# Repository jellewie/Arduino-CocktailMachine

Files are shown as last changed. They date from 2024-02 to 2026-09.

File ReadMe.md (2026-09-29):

# **Cocktail Mixer Machine**  
_A machine that can mix drinks_

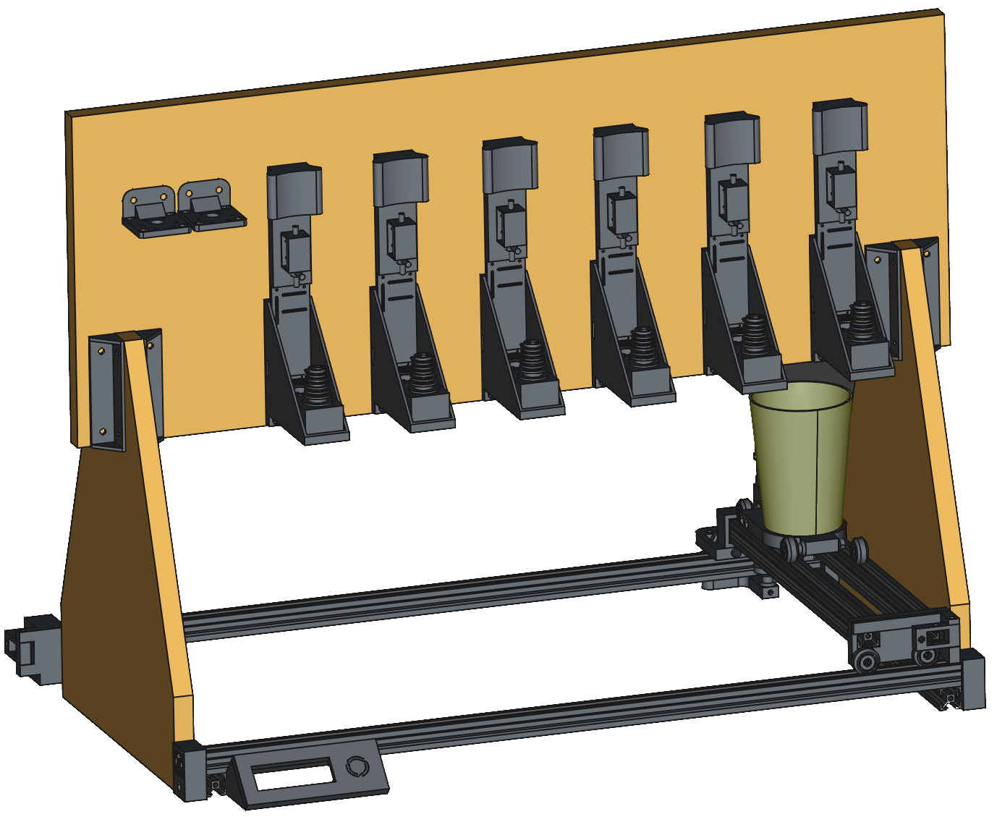
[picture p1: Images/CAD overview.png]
Cocktail Mixer Machine CAD


Part of this project is sponsored by [PCBWay](https://www.pcbway.com/). Read more about that [here](Sponsorship.md).

## **Firmware**
> **Note**: This project is still in development!

### Compile
- [Arduino sketch](Arduino) The whole sketch is the 'Arduino' folder.
- [ESP32](https://dl.espressif.com/dl/package_esp32_index.json) must be added as an additional board manager in Arduino IDE.
- [FastLED](https://github.com/FastLED/FastLED) can be downloaded through the built-in library manager in Arduino IDE.
- [AccelStepper](https://github.com/waspinator/AccelStepper) can be downloaded through the built-in library manager in Arduino IDE.
- [LiquidCrystal_I2C](https://github.com/johnrickman/LiquidCrystal_I2C) can be downloaded through the built-in library manager in Arduino IDE.
- [Deno](https://deno.land/) to re-compile the webpage.
- [Arduino-WIFIManager](https://github.com/jellewie/Arduino-WiFiManager) (already included).
- [Arduino-Button](https://github.com/jellewie/Arduino-Button) (already included).
- [Arduino-Stable-analog-read](https://github.com/jellewie/Arduino-Stable-analog-read) (already included).
- [FreeCAD](https://github.com/FreeCAD/FreeCAD) is used for 3D modeling.
- [A2Plus_Workbench](https://github.com/kbwbe/A2plus) is used for creating the assembly.

To custom compile with new drinks and such, update the drinks in [Website/src/drinksConfig.js](Website/src/drinksConfig.js). I use an automated Google Drive sheet for this.

To update the Arduino to use this, run "deno task build" in the command prompt. This will update the client.h, after which you can start Arduino IDE and use it.

### BIN
Uploading a BIN file with a cable to the ESP can be done by any [ESP32 BIN file uploader](https://www.espressif.com/en/support/download/other-tools). this step is required for the first flash time.

## Webpage
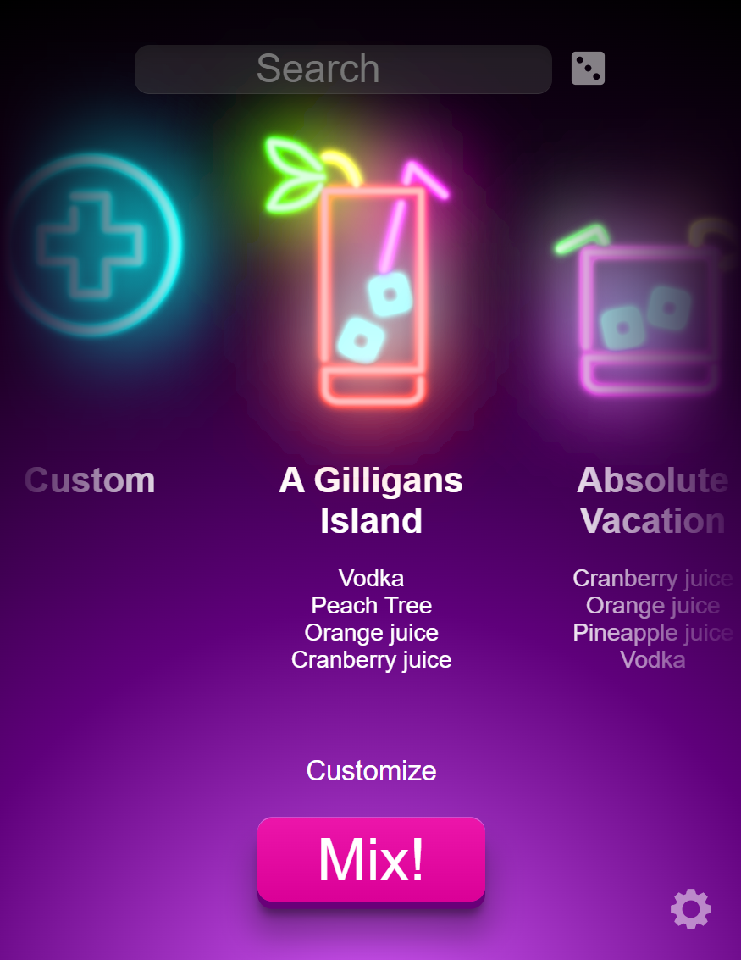
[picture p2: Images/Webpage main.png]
The landing webpage of the machine

The machine makes its own fancy landing page. This page has a lot going for it, First of all, are the items sorted on last used (this is done locally per user device). But the page has also a lot of functions, for example, it has a search bar to search for the name, but it also has a dice function to select a random mix.

After you have chosen your mix, you can directly start mixing, or you can Customize the drink to your liking

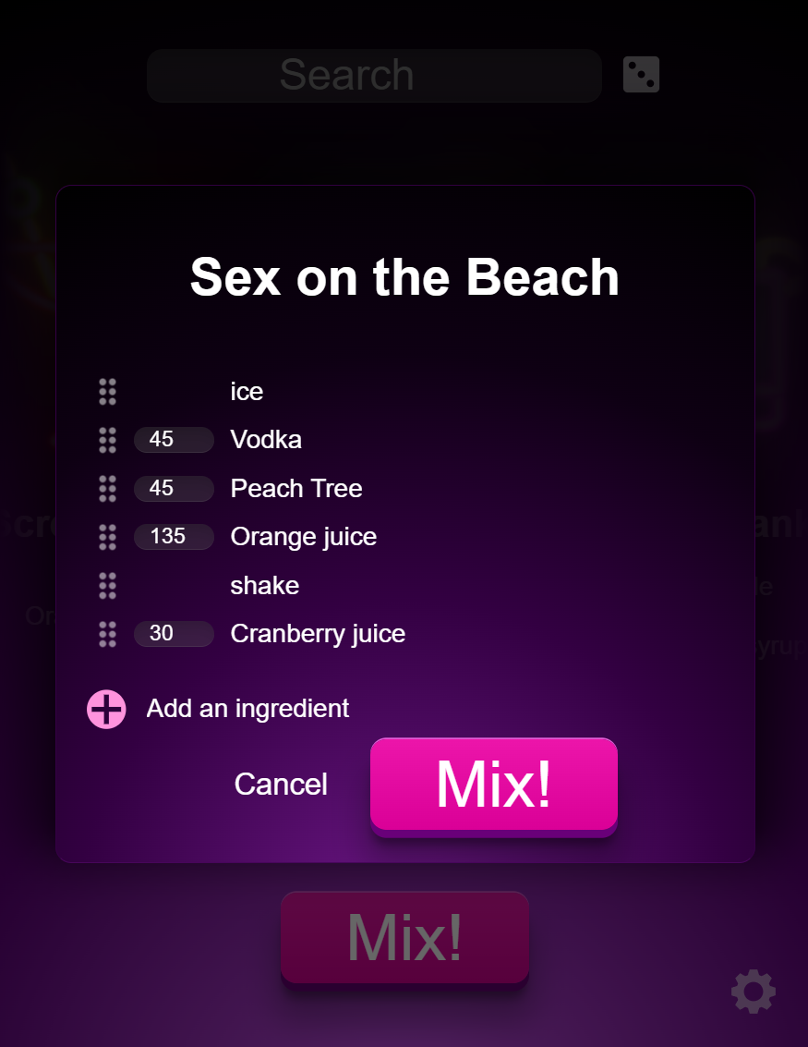
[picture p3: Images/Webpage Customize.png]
Customize drink

It also has a settings page

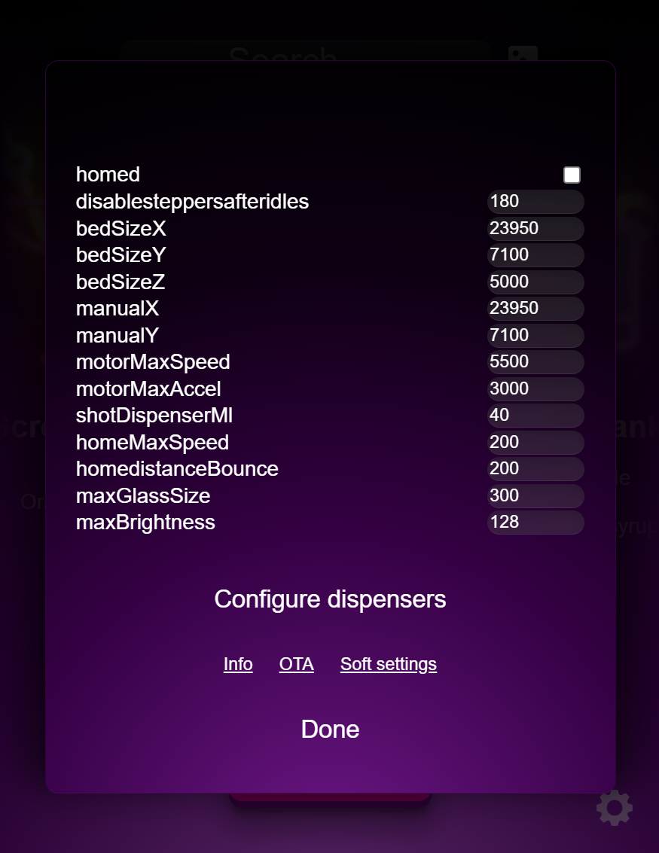
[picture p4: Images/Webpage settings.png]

This is also where the dispensers are configured

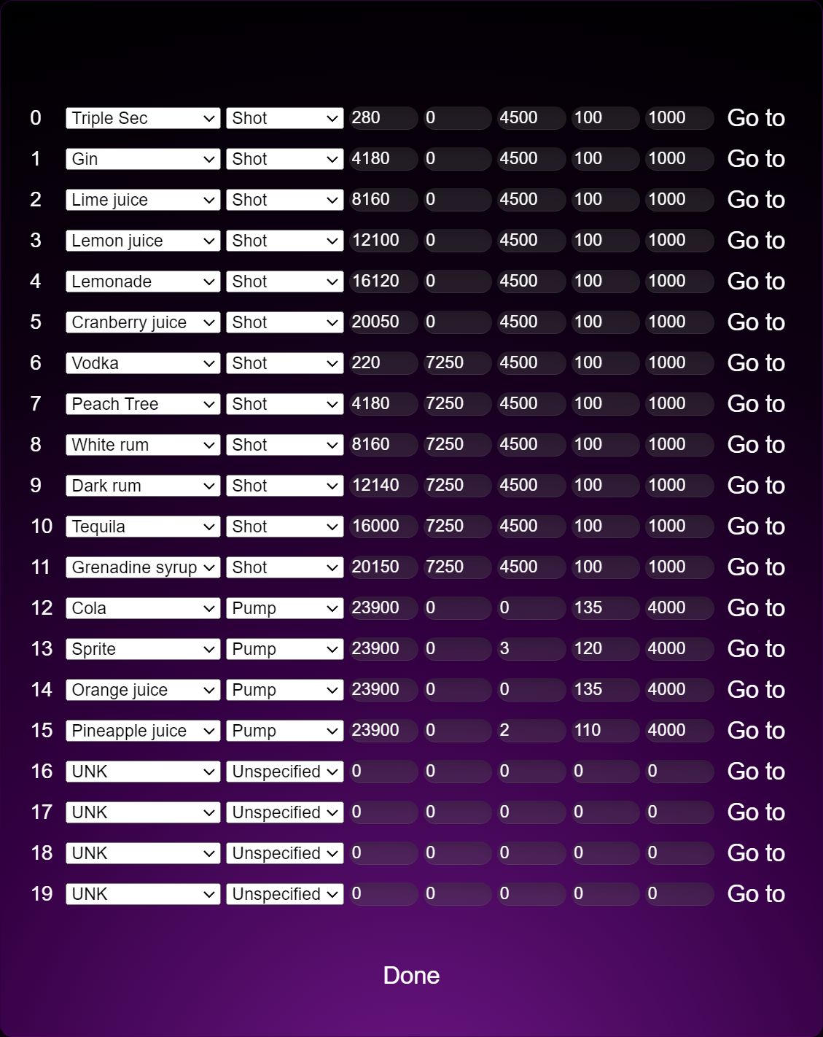
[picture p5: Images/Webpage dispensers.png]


## LED status

## WIFI page
The 2 most important pages are the [Setup](#setup) page, where the user can set up the mixer. And the [main landing page](#control) where the fancy UI is.
Setup is only really needed once during the setup of WiFi in Apmode, because in runtime the mixer settings can be adjusted in the main UI.

### Setup
The setup page will be accessible and shown in APmode, but can also be accessed by going to [mixer.local/ip](http://mixer.local/ip). 
The password is replaced with starts, and cannot be received without changing the firmware. 
Leave fields blank (or for the password leaving only stars) to not update those values upon sending this forum, set on space ' ' to clear them.
By default the SSID and password are limited to 16 characters by the firmware, and the total bytes that can be stored in memory is limited to 4096. Going over these values results in unexpected behavior. 

### Getting it’s IP
User devices that support mDNS, like Windows and Apple, can use [mixer.local/info](http://mixer.local/info) to obtain its IP.

Alternatively in a lot of stages (like after boot) the IP will be shown on the display.

### Control
The control page is the default landing page the user will land on. Here you select, customize, and mix the selected drink. 

- **customize** Will give a pop-up window to customize and mix your drink.
- **MIX** Will start mixing it right away.
- **Settings button** The gear on the right lower corner will open the settings page.

#### Settings button
- Some [Soft settings](#Soft-settings) are exposed here
- **OTA** will direct to the [OTA](#ota-over-the-air-update) update page, where the firmware can be updated over the WiFi.
- **Reset** will fully restart the ESP.
- **Info** will open the info page with some information like the version compile date.
- **Saved settings** just redirects you to [mixer.local/ip](http://mixer.local/ip) to show you the values saved in the EEPROM.

### Soft settings

### OTA (Over The Air update)
This page can be accessed on [mixer.local/ota](http://mixer.local/ota) (or 'IP/ota') and enables you to update firmware over WiFi.
On this page is a 'choose file' button where the new version can be selected. Make sure the right, compatible, most updated file is selected ("Mixer.bin"). This can be downloaded from [releases](https://github.com/jellewie/Arduino-CocktailMachine/releases). 
After which the 'Upload' button needs to be pressed for the update process to begin, the unit will automatically update and reboot afterward.
Note that [SoftSettings](#soft-settings) are preserved.

### Full reset
If a full reset is desired it can be achieved by going to 'mixer.local/reset'. But note that accessing the page will directly wipe all [SoftSettings](#soft-settings) from existence and there will be no way to restore them back. If the wipe was successful it will be reported back and will execute a restart.

# Appendix
* Firmware
[This is included in this repository](Arduino)
* PCB & schematic
[This is included in this repository](Schematic-PCB)
Beta/ updated version on [EasyEDA](https://easyeda.com/selbiekoekie/cocktail-machine)
* BOM
[This is included in this repository](BOM.md)

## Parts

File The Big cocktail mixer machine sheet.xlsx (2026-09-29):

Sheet: BOM
Description | Amount | Comments | Link buy | Link info | Piece price | Shipping | Total | |Description|Amount|Comments|Link buy|Link info|Piece price|Shipping|Total
--- | --- | --- | --- | --- | --- | --- | --- | |---|---|---|---|---|---|---|---
Peristaltic Pump,12V (We use zy-1000f5) | 4 | Only needed for carbonated liquids | https://www.banggood.com/500mL-or-min-Large-Flow-Easy-To-Install-Peristaltic-Pump-12V-or-24V-Metering-Vacuum-Pump-Flat-Type-Aquarium-p-1749029.html https://nl.aliexpress.com/item/1005004441796531.html | https://youtu.be/AMiXme4bMUk | €25.95 | €1.62 | €105.40 | |Peristaltic Pump,12V (We use zy-1000f5)|4|Only needed for carbonated liquids|[link](https://www.banggood.com/500mL-or-min-Large-Flow-Easy-To-Install-Peristaltic-Pump-12V-or-24V-Metering-Vacuum-Pump-Flat-Type-Aquarium-p-1749029.html https://nl.aliexpress.com/item/1005004441796531.html|[link](https://youtu.be/AMiXme4bMUk)|25.95|1.62|105.4
Pullys | 2 |  | https://www.123-3d.nl/123-3D-GT2-Pulley-hoge-resolutie-met-lager-6-mm-riem-20-tanden-5-mm-as-zwart-i2546-t0.html |  | €7.50 | €0.71 | €15.71 | |Pullys|2||[link](https://www.123-3d.nl/123-3D-GT2-Pulley-hoge-resolutie-met-lager-6-mm-riem-20-tanden-5-mm-as-zwart-i2546-t0.html)||7.5|0.71|15.71
Motor pullys | 2 |  | https://www.123-3d.nl/123-3D-GT2-Pulley-hoge-resolutie-6-mm-riem-20-tanden-5-mm-as-zwart-400211009-i2547-t0.html |  | €7.50 | €0.71 | €15.71 | |Motor pullys|2||[link](https://www.123-3d.nl/123-3D-GT2-Pulley-hoge-resolutie-6-mm-riem-20-tanden-5-mm-as-zwart-400211009-i2547-t0.html)||7.5|0.71|15.71
Reininforced belt 6mm wide | 1 | 2.7m needed | https://www.123-3d.nl/123-3D-GT2-timing-belt-6-mm-5-meter-i6541-t3046.html |  | €21.00 | €0.71 | €21.71 | |Reininforced belt 6mm wide|1|2.7m needed|[link](https://www.123-3d.nl/123-3D-GT2-timing-belt-6-mm-5-meter-i6541-t3046.html)||21|0.71|21.71
Leadscrew moer, TR8x8 | 1 |  | https://www.123-3d.nl/123-3D-Leadscrew-moer-TR8x8-i1560-t0.html |  | €6.00 | €0.71 | €6.71 | |Leadscrew moer, TR8x8|1||[link](https://www.123-3d.nl/123-3D-Leadscrew-moer-TR8x8-i1560-t0.html)||6|0.71|6.71
Leadscrew, TR8x8, 8 mm | 1 | This one is 30cm, unsure what we need | https://www.123-3d.nl/123-3D-Leadscrew-TR8x8-8-mm-30-cm-i1558-t0.html |  | €9.50 | €0.71 | €10.21 | |Leadscrew, TR8x8, 8 mm|1|This one is 30cm, unsure what we need|[link](https://www.123-3d.nl/123-3D-Leadscrew-TR8x8-8-mm-30-cm-i1558-t0.html)||9.5|0.71|10.21
Staaf as glad 8 m | 1 | This one is 100cm, unsure what we need | https://www.123-3d.nl/123-3D-Staaf-as-glad-8-mm-x-100-cm-voor-X-of-Y-as-i56-t0.html |  | €3.75 | €0.71 | €4.46 | |Staaf as glad 8 m|1|This one is 100cm, unsure what we need|[link](https://www.123-3d.nl/123-3D-Staaf-as-glad-8-mm-x-100-cm-voor-X-of-Y-as-i56-t0.html)||3.75|0.71|4.46
Flexibele motor koppeling 5 mm - 8 mm | 1 |  | https://www.123-3d.nl/123-3D-Flexibele-motor-koppeling-5-mm-8-mm-i342-t0.html |  | €4.50 | €0.71 | €5.21 | |Flexibele motor koppeling 5 mm - 8 mm|1||[link](https://www.123-3d.nl/123-3D-Flexibele-motor-koppeling-5-mm-8-mm-i342-t0.html)||4.5|0.71|5.21
Frame end caps 2020 (3d print) | 10 | Print in black |  | https://www.thingiverse.com/thing:2393904 | €0.02 | €0.00 | €0.20 | |Frame end caps 2020 (3d print)|10|Print in black||[link](https://www.thingiverse.com/thing:2393904)|0.02|0|0.2
Drink dispensers (6 way) | 2 | Spraypaint black | https://www.bol.com/nl/nl/p/white-rhinoceros-drank-dispenser-bar-butler-shots-muurdispenser-voor-6-flessen/9300000007705748/ |  | €38.95 | €0.00 | €77.90 | |Drink dispensers (6 way)|2|Spraypaint black|[link](https://www.bol.com/nl/nl/p/white-rhinoceros-drank-dispenser-bar-butler-shots-muurdispenser-voor-6-flessen/9300000007705748/||38.95|0|77.9
V frame (black 1500mm) | 2 | Cut in sizes: 2x750 + 2x353.5 + 2x396.5mm | https://www.ratrig.com/aluminium-profiles/vslot/v-slot-2020-637.html |  | €12.54 | €28.52 | €53.60 | |V frame (black 1500mm)|2|Cut in sizes: 2x750 + 2x353.5 + 2x396.5mm|[link](https://www.ratrig.com/aluminium-profiles/vslot/v-slot-2020-637.html)||12.54|28.52|53.6
Frame corner profiles | 20 |  | https://nl.aliexpress.com/item/1005003618509458.html |  | €0.50 | €2.43 | €12.45 | |Frame corner profiles|20||[link](https://nl.aliexpress.com/item/1005003618509458.html)||0.5|2.43|12.45
Wood (Gamma) | 1 | 2x30x80cm |  |  | €30.48 | €0.00 | €30.48 | |Wood (Gamma)|1|2x30x80cm|||30.48|0|30.48
16x2 LCD Display I2C | 1 |  | https://elektronicavoorjou.nl/product/16x2-lcd-wit-op-blauw-5v-met-i2c/ |  | €9.95 | €2.99 | €12.94 | |16x2 LCD Display I2C|1||[link](https://elektronicavoorjou.nl/product/16x2-lcd-wit-op-blauw-5v-met-i2c/)||9.95|2.99|12.94
M3x10 | 50 |  | https://www.indi.nl/nl-nl/p/Cilindrische-inbusbout-M3x10-12.9-zwart-DIN912-912310129B |  | €0.17 | €1.40 | €10.02 | |M3x10|50||[link](https://www.indi.nl/nl-nl/p/Cilindrische-inbusbout-M3x10-12.9-zwart-DIN912-912310129B)||0.17|1.4|10.02
M3x30 | 50 |  | https://www.indi.nl/nl-nl/p/Cilindrische-inbusbout-M3x30-12.9-zwart-DIN912-912330129B |  | €0.17 | €1.40 | €10.02 | |M3x30|50||[link](https://www.indi.nl/nl-nl/p/Cilindrische-inbusbout-M3x30-12.9-zwart-DIN912-912330129B)||0.17|1.4|10.02
M5x10 | 50 |  | https://www.indi.nl/nl-nl/p/Cilindrische-inbusbout-M5x10-12.9-zwart-DIN912-912510129B |  | €0.18 | €1.40 | €10.40 | |M5x10|50||[link](https://www.indi.nl/nl-nl/p/Cilindrische-inbusbout-M5x10-12.9-zwart-DIN912-912510129B)||0.18|1.4|10.4
M5x20 | 50 |  | https://www.indi.nl/nl-nl/p/Cilindrische-inbusbout-M5x20-12.9-zwart-DIN912-912520129B |  | €0.18 | €1.40 | €10.40 | |M5x20|50||[link](https://www.indi.nl/nl-nl/p/Cilindrische-inbusbout-M5x20-12.9-zwart-DIN912-912520129B)||0.18|1.4|10.4
M5x30 | 50 |  | https://www.indi.nl/nl-nl/p/Cilindrische-inbusbout-M5x30-12.9-zwart-DIN912-912530129B |  | €0.18 | €1.40 | €10.40 | |M5x30|50||[link](https://www.indi.nl/nl-nl/p/Cilindrische-inbusbout-M5x30-12.9-zwart-DIN912-912530129B)||0.18|1.4|10.4
M5x40 | 50 |  | https://www.indi.nl/nl-nl/p/Cilindrische-inbusbout-M5x40-12.9-zwart-DIN912-912540129B |  | €0.27 | €1.40 | €14.90 | |M5x40|50||[link](https://www.indi.nl/nl-nl/p/Cilindrische-inbusbout-M5x40-12.9-zwart-DIN912-912540129B)||0.27|1.4|14.9
M5x50 | 50 |  | https://www.indi.nl/nl-nl/p/Cilindrische-inbusbout-M5X50-12.9-zwart-DIN912-912550129B |  | €0.34 | €1.40 | €18.40 | |M5x50|50||[link](https://www.indi.nl/nl-nl/p/Cilindrische-inbusbout-M5X50-12.9-zwart-DIN912-912550129B)||0.34|1.4|18.4
M5x60 | 50 |  | https://www.indi.nl/nl-nl/p/Cilindrische-inbusbout-M5x60-12.9-zwart-DIN912-912560129B |  | €0.39 | €1.40 | €20.72 | |M5x60|50||[link](https://www.indi.nl/nl-nl/p/Cilindrische-inbusbout-M5x60-12.9-zwart-DIN912-912560129B)||0.39|1.4|20.72
M5x80 | 50 |  | https://www.indi.nl/nl-nl/p/Cilindrische-inbusbout-M5x80-12.9-zwart-DIN912-912580129B |  | €0.84 | €1.40 | €43.16 | |M5x80|50||[link](https://www.indi.nl/nl-nl/p/Cilindrische-inbusbout-M5x80-12.9-zwart-DIN912-912580129B)||0.84|1.4|43.16
Moer | 200 |  | https://www.indi.nl/nl-nl/p/Zeskantmoer-M5-klasse-8-verzinkt-DIN934-9345P100 |  | €0.05 | €1.40 | €11.40 | |Moer|200||[link](https://www.indi.nl/nl-nl/p/Zeskantmoer-M5-klasse-8-verzinkt-DIN934-9345P100)||0.05|1.4|11.4
Borgmoer | 8 |  | https://www.gamma.nl/assortiment/gamma-borgmoer-m5-rvs-8-stuks/p/B458288 |  | €0.35 | €0.00 | €2.79 | |Borgmoer|8||[link](https://www.gamma.nl/assortiment/gamma-borgmoer-m5-rvs-8-stuks/p/B458288)||0.35|0|2.79
V-slot wheels | 11 |  |  |  | €0.71 | €0.00 | €7.83 | |V-slot wheels|11||||0.71|0|7.83
JLC PCB | 5 | (minimum 5 pieces) |  |  | €1.44 | €0.00 | €7.20 | |JLC PCB|5|(minimum 5 pieces)||[link]()|1.44|0|7.2
PCB-TMC2208 motor controller | 3 | X, Y, Z | https://nl.aliexpress.com/item/1005004014058136.html | https://wiki.fysetc.com/TMC2208/ | €2.49 | €0.00 | €7.46 | |PCB-TMC2208 motor controller|3|X, Y, Z|[link](https://nl.aliexpress.com/item/1005004014058136.html)|[link](https://wiki.fysetc.com/TMC2208/)|2.49|0|7.46
Microswitch | 3 | Used for homing, not as limit switch | https://www.hobbyelectronica.nl/product/endstop-mechanisch-microswitch/ |  | €0.95 | €3.45 | €6.30 | |Microswitch|3|Used for homing, not as limit switch|[link](https://www.hobbyelectronica.nl/product/endstop-mechanisch-microswitch/)||0.95|3.45|6.3
Tubing 5x7 | 6 |  | https://www.kiwi-electronics.com/nl/siliconen-slang-5x7mm-2-meter-10188 |  | €1.95 | €2.95 | €14.65 | |Tubing 5x7|6||[link](https://www.kiwi-electronics.com/nl/siliconen-slang-5x7mm-2-meter-10188)||1.95|2.95|14.65
Tubing 2x4 | 14 |  | https://www.slangenshop.nl/home/22-siliconen-slang-2-x-4-mm-.html |  | €2.22 | €7.95 | €39.03 | |Tubing 2x4|14||[link](https://www.slangenshop.nl/home/22-siliconen-slang-2-x-4-mm-.html)||2.22|7.95|39.03
Tubing 3x5 | 7 |  | https://www.slangenshop.nl/home/25-siliconen-slang-3-x-5-mm-.html |  | €3.88 | €6.95 | €34.11 | |Tubing 3x5|7||[link](https://www.slangenshop.nl/home/25-siliconen-slang-3-x-5-mm-.html)||3.88|6.95|34.11
Tubing 4x6 | 7 |  | https://www.slangenshop.nl/home/24-siliconen-slang-4-x-6-mm-.html?search_query=Siliconen+slang+4&results=24 |  | €3.81 | €7.95 | €34.62 | |Tubing 4x6|7||[link](https://www.slangenshop.nl/home/24-siliconen-slang-4-x-6-mm-.html?search_query=Siliconen+slang+4&results=24)||3.81|7.95|34.62
0826B 0.5-20N 8mm | 1 |  | https://www.aliexpress.com/item/1005004016711403.html?spm=a2g0o.cart.0.0.603638daNtRRN5&mp=1 |  | €8.54 |  | €8.54 | |0826B 0.5-20N 8mm|1||[link](https://www.aliexpress.com/item/1005004016711403.html?spm=a2g0o.cart.0.0.603638daNtRRN5&mp=1)||8.54||8.54
1050B 4.5-50N 15mm | 1 |  | https://www.aliexpress.com/item/1005004016711403.html?spm=a2g0o.cart.0.0.603638daNtRRN5&mp=1 |  | €16.36 |  | €16.36 | |1050B 4.5-50N 15mm|1||[link](https://www.aliexpress.com/item/1005004016711403.html?spm=a2g0o.cart.0.0.603638daNtRRN5&mp=1)||16.36||16.36
Motion Film Pressure Sensor 100g | 1 |  | https://www.aliexpress.com/item/32878178151.html?spm=a2g0o.cart.0.0.603638daNtRRN5&mp=1 |  | €1.31 | €0.80 | €2.10 | |Motion Film Pressure Sensor 100g|1||[link](https://www.aliexpress.com/item/32878178151.html?spm=a2g0o.cart.0.0.603638daNtRRN5&mp=1)||1.31|0.8|2.11
Motion Film Pressure Sensor 1kg | 1 |  | https://www.aliexpress.com/item/32878178151.html?spm=a2g0o.cart.0.0.603638daNtRRN5&mp=1 |  | €1.31 | €0.80 | €2.10 | |Motion Film Pressure Sensor 1kg|1||[link](https://www.aliexpress.com/item/32878178151.html?spm=a2g0o.cart.0.0.603638daNtRRN5&mp=1)||1.31|0.8|2.11
Solenoid Valve 4.5mm inner 12V | 1 |  | https://www.aliexpress.com/item/1005005553905520.html?spm=a2g0o.cart.0.0.603638daNtRRN5&mp=1 |  | €3.34 | €3.61 | €6.95 | |Solenoid Valve 4.5mm inner 12V|1||[link](https://www.aliexpress.com/item/1005005553905520.html?spm=a2g0o.cart.0.0.603638daNtRRN5&mp=1)||3.34|3.61|6.95
CNC W202502152128202 | 1 |  |  |  | €39.93 |  | €39.93 | |CNC W202502152128202|1||||39.93||39.93
CNC W202410082342933 |  |  |  |  | €43.10 |  | €0.00 | |CNC W202410082342933|||||43.1||0
CNC CNC2403305000117-2352374A |  |  |  |  | €19.99 |  | €0.00 | |CNC CNC2403305000117-2352374A|||||19.99||0
 |  |  |  |  |  |  | €0.00
 |  |  |  |  |  |  | €0.00
 |  |  |  |  |  |  | €0.00
 |  |  |  |  |  |  | €0.00
SUBTOTAAL |  |  |  |  |  |  | €762.48
Steppermotor | 3 | We actually use 1.8deg 2.4Ohm | https://www.hobbyelectronica.nl/product/nema-17-stappen-motor-42byghw609/ |  | €22.62 | €6.95 | €74.81 | |Steppermotor|3|We actually use 1.8deg 2.4Ohm|[link](https://www.hobbyelectronica.nl/product/nema-17-stappen-motor-42byghw609/||22.62|6.95|74.81
Connector MTA-100-2P | 7 |  |  |  | €0.15 |  | €1.04 | |Connector MTA-100-2P|7|||[link]()|0.15||1.04
Connector MTA-100-3P | 1 |  |  |  | €0.14 |  | €0.14 | |Connector MTA-100-3P|1|||[link]()|0.14||0.14
Connector MTA-100-4P | 4 |  |  |  | €0.23 |  | €0.94 | |Connector MTA-100-4P|4|||[link]()|0.24||0.94
Connector MTA-156-2P | 2 |  |  |  | €0.22 |  | €0.44 | |Connector MTA-156-2P|2||||0.22||0.44
PCB-MTA-100-2P | 7 | H2,H3,H4,H11,H12,H13,H14 |  |  | €0.10 |  | €0.73 | |PCB-MTA-100-2P|7|H2,H3,H4,H11,H12,H13,H14||[link]()|0.11||0.74
PCB-MTA-100-3P | 1 | for LED D=H5 | http://www.te.com/commerce/DocumentDelivery/DDEController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 |  | €0.07 |  | €0.07 | |PCB-MTA-100-3P|1|for LED D=H5|[link](http://www.te.com/commerce/DocumentDelivery/DDEController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)||0.07||0.07
PCB-MTA-100-4P | 4 | H8, H9, H10,H16 | http://www.te.com/commerce/DocumentDelivery/DDEController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 |  | €0.13 |  | €0.51 | |PCB-MTA-100-4P|4|H8, H9, H10,H16|[link](http://www.te.com/commerce/DocumentDelivery/DDEController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)||0.13||0.51
PCB-MTA-156-2P | 2 | H6, H7 |  |  | €0.10 |  | €0.21 | |PCB-MTA-156-2P|2|H6, H7||[link]()|0.11||0.21
PCB-L2203N | 4 | Q1,Q2,Q3,Q4 |  |  | €0.93 |  | €3.73 | |PCB-L2203N|4|Q1,Q2,Q3,Q4|[link]( )|[link]()|0.93||3.73
PCB-C0805 100nF | 6 | C1,C2,C3,C4,C5,C6 |  |  | €0.01 |  | €0.05 | |PCB-C0805 100nF|6|C1,C2,C3,C4,C5,C6|[link]( )|[link]()|0.01||0.05
PCB-R0805 1k | 7 | R1,R2,R3,R4,R5,R6,R7 |  |  | €0.01 |  | €0.05 | |PCB-R0805 1k|7|R1,R2,R3,R4,R5,R6,R7|[link]( )|[link]()|0.01||0.05
PCB-R0805 100R | 1 | R8 |  |  | €0.01 |  | €0.01 | |PCB-R0805 100R|1|R8|[link]( )|[link]()|0.01||0.01
PCB-R0805 10R | 1 | R9 |  |  | €0.01 |  | €0.01 | |PCB-R0805 10R|1|R9|[link]( )|[link]()|0.01||0.01
PCB-DOIT ESP32 DEVKIT V1 | 1 | U1 |  |  | €3.96 |  | €3.96 | |PCB-DOIT ESP32 DEVKIT V1|1|U1|[link]( )|[link]()|3.96||3.96
PCB-R78B5020 | 1 | U2 | https://nl.farnell.com/recom-power/r-78b5-0-1-0l/dc-dc-converter-5v-1a/dp/1793162 |  | €7.57 |  | €7.57 | |PCB-R78B5020|1|U2|[link](https://nl.farnell.com/recom-power/r-78b5-0-1-0l/dc-dc-converter-5v-1a/dp/1793162)||7.57||7.57
PCB-SIL header | 2 | Steppers, H1 |  |  | €0.06 | €0.00 | €0.12 | |PCB-SIL header|2|Steppers, H1||[link]()|0.06|0|0.12
12V power supply | 1 |  |  |  |  |  | €0.00 | |12V power supply|1||||||0
Wires |  |  |  |  |  |  | €0.00 | |Wires|||||||0
Wire sleeves? |  |  |  |  |  |  | €0.00 | |Wire sleeves?|||||||0
PCBway Dispensers | 13 |  |  |  | €85.36 |  | €1109.68 | |PCBway Dispensers|13|||[link]()|85.36||1109.68
0805 4.7UH | 50 |  | https://nl.aliexpress.com/item/1005006311167114.html |  |  |  | €0.00 | |0805 4.7UH|50||[link](https://nl.aliexpress.com/item/1005006311167114.html||||0
heatshrink | 2 |  | https://nl.aliexpress.com/item/1005006321995370.html |  | €1.79 |  | €3.58 | |heatshrink|2||[link](https://nl.aliexpress.com/item/1005006321995370.html||1.79||3.58
Diode IN4007 | 100 |  | www.aliexpress.com/item/1005006852412154.html?spm=a2g0o.order_list.order_list_main.33.3f8379d22lLZlI |  | €0.04 |  | €3.50 | |Diode IN4007|100||[link](www.aliexpress.com/item/1005006852412154.html||0.04||3.5
ESP32 C3 | 20 |  | https://nl.aliexpress.com/item/1005007446928015.html |  | €1.04 |  | €20.81 | |ESP32 C3|20||[link](https://nl.aliexpress.com/item/1005007446928015.html||1.04||20.81
Dispenser magnet | 25 |  | https://nl.aliexpress.com/item/1005006531774076.html |  | €2.69 |  | €67.20 | |Dispenser magnet|25||[link](https://nl.aliexpress.com/item/1005006531774076.html||2.69||67.2
O-rings dispenserbold | 675 |  | https://nl.aliexpress.com/item/1005008478445571.html |  | €0.01 |  | €8.82 | |O-rings dispenserbold|675||[link](https://nl.aliexpress.com/item/1005008478445571.html||0.01||8.82
M5 bolt 5mm | 20 |  | https://nl.aliexpress.com/item/32810872544.html |  | €0.11 |  | €2.18 | |M5 bolt 5mm|20||[link](https://nl.aliexpress.com/item/32810872544.html||0.11||2.18
M4 bolt 10mm | 60 |  | https://nl.aliexpress.com/item/32810872544.html |  | €0.07 |  | €4.04 | |M4 bolt 10mm|60||[link](https://nl.aliexpress.com/item/32810872544.html||0.07||4.04
M3 bolt 5mm | 200 |  |  |  | €0.02 |  | €4.04 | |M3 bolt 5mm|200||||0.02||4.04
Capacitor 47uF | 50 |  | www.aliexpress.com/item/1005002047657907.html |  | €0.04 |  | €2.15 | |Capacitor 47uF |50||[link](www.aliexpress.com/item/1005002047657907.html||0.04||2.15
8 DIP header | 60 |  | https://www.aliexpress.com/item/1005006995121970.html |  | €0.03 |  | €1.51 | |8 DIP header|60||[link](https://www.aliexpress.com/item/1005006995121970.html||0.03||1.51
Pin headeer | 20 |  | https://nl.aliexpress.com/item/1005006149080284.html |  | €0.12 |  | €2.36 | |Pin headeer|20||[link](https://nl.aliexpress.com/item/1005006149080284.html||0.12||2.36
Mini valves | 16 |  | https://www.aliexpress.com/item/1005006358997795.html |  | €2.44 |  | €39.08 | |Mini valves|16||[link](https://www.aliexpress.com/item/1005006358997795.html||2.44||39.08
transistor AO3416 | 100 |  | https://www.aliexpress.com/item/1005005013827080.html |  | €0.02 |  | €2.03 | |transistor AO3416|100||[link](https://www.aliexpress.com/item/1005005013827080.html||0.02||2.03
Diode LL4148 | 100 |  | https://nl.aliexpress.com/item/1005002748966091.html |  | €0.02 |  | €1.63 | |Diode LL4148|100||[link](https://nl.aliexpress.com/item/1005002748966091.html||0.02||1.63
Rubber bottle end piece | 20 |  | https://www.bol.com/nl/nl/p/kurk-zwart-pe-in-perfect-afsluitende-vorm-tbv-non-drips-of-maatschenkers-ten-behoeve-van-0-7-1-5-l-flessen/9200000107083693/ |  | €0.99 |  | €19.90 | |Rubber bottle end piece|20||[link](https://www.bol.com/nl/nl/p/kurk-zwart-pe-in-perfect-afsluitende-vorm-tbv-non-drips-of-maatschenkers-ten-behoeve-van-0-7-1-5-l-flessen/9200000107083693/)||1||19.9
3D prints | 1 |  |  |  | €34.72 |  | €34.72 | |3D prints|1||||34.72||34.72
Valve 46.008.116 | 13 |  | https://www.libertyshop.de/Magnetventile/A-u-K--Mueller/Blockventile----Vending/Serie-46-008-x16---Ventile/Mueller-Blockventil-1-fach-24-V-AC-46-008-116-Neue-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 |  | €33.35 | €17.85 | €451.36 | |Valve 46.008.116|13||[link](https://www.libertyshop.de/Magnetventile/A-u-K--Mueller/Blockventile----Vending/Serie-46-008-x16---Ventile/Mueller-Blockventil-1-fach-24-V-AC-46-008-116-Neue-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||33.35|17.85|451.36
 |  |  |  |  |  |  | €0.00
 |  |  |  |  |  |  | €0.00
 |  |  |  |  |  |  | €0.00
TOTAAL |  |  |  |  |  |  | €2635.48

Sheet: Pinout
GPIO | Input | Output | Notes
0 | pulled up | OK | outputs PWM signal at boot | NU | was
1 | TX pin | OK | debug output at boot | TX
2 | OK | OK | connected to on-board LED | LED
3 | OK | RX pin | HIGH at boot | RX
4 | OK | OK |  | PDO_X_Step
5 | OK | OK | outputs PWM signal at boot | PDI_X_Ref | PDO_Y_Step
12 | OK | OK | boot fail if pulled high | PDO_Y_Step | PDI_X_Ref
13 | OK | OK |  | LED_PWM
14 | OK | OK | outputs PWM signal at boot | PDI_B
15 | OK | OK | outputs PWM signal at boot | PDI_Z_Ref | PDO_X_Dir
16 | OK | OK |  | PDO_Step_enable
17 | OK | OK |  | PDO_Y_Dir
18 | OK | OK |  | PDO_Z_Dir
19 | OK | OK |  | PDO_Z_Step
21 | OK | OK |  | I2C_SDA
22 | OK | OK |  | I2C_SCL
23 | OK | OK |  | PDO_X_Dir
25 | OK | OK |  | PDO_Pump3
26 | OK | OK |  | PDO_Pump4
27 | OK | OK |  | PDI_Y_Ref | PDI_A
32 | OK | OK |  | PDO_Pump1
33 | OK | OK |  | PDO_Pump2
34 | OK |  | input only | PDI_A | PDI_Y_Ref
35 | OK |  | input only |  | PDI_Z_Ref
36 | OK |  | input only
39 | OK |  | input only | PDI_S

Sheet: Drinks
Cocktail | Color | Ingredient 1 | ml | Ingredient 2 | ml | Ingredient 3 | ml | Ingredient 4 | ml | Ingredient 5 | ml | Ingredient 6 | ml | Ingredient 7 | ml | Ingredient 8 | ml | ml total | Glass
Sex on the Beach | bab34 | #ice | 0 | Vodka | 45 | Peach Tree | 45 | Orange juice | 135 | #shake | 0 | Cranberry juice | 30 |  |  |  |  | 255 | Big
Screwdriver | e8d86d | Vodka | 45 | Orange Juice | 120 | #stir | 0 |  |  |  |  |  |  |  |  |  |  | 165 | Medium
Cosmopolitan Classic | e81058 | Vodka | 23 | Triple Sec | 15 | Cranberry juice | 30 | Lime juice | 15 | #shake | 0 |  |  |  |  |  |  | 83 | Rock
Bay Breeze | ff8400 | Vodka | 45 | Pineapple juice | 30 | Cranberry juice | 30 | #stir | 0 |  |  |  |  |  |  |  |  | 105 | Rock
Hole in One | e3c532 | #ice | 0 | Vodka | 45 | Cranberry juice | 90 | #stir | 0 | Orange juice | 30 |  |  |  |  |  |  | 165 | Medium
Gimlet | d5f5dd | #crushed ice | 0 | Gin | 90 | Lime juice | 30 | #shake | 0 |  |  |  |  |  |  |  |  | 120 | Medium
Black widow | 800101 | Vodka | 30 | Cranberry juice | 30 | Lemonade | 30 | #stir | 0 |  |  |  |  |  |  |  |  | 90 | Rock
Gin Sidecar | ced190 | #crushed ice | 0 | Gin | 60 | Triple sec | 30 | Lemon juice | 30 | #shake | 0 |  |  |  |  |  |  | 120 | Medium
Little Devil | db4f40 | #crushed ice | 0 | Gin | 60 | White rum | 45 | Triple sec | 30 | Lemon juice | 30 | #shake | 0 |  |  |  |  | 165 | Medium
Hoola Hoop | e3bc5b | Gin | 45 | Orange Juice | 30 | Pineapple juice | 30 | #stir | 0 |  |  |  |  |  |  |  |  | 105 | Rock
Hawaiian Cocktail | edc766 | Gin | 60 | Triple Sec | 15 | Pineapple juice | 15 | #shake | 0 |  |  |  |  |  |  |  |  | 90 | Rock
Alpine Lemonade | f5e4bc | #ice | 0 | Vodka | 30 | Gin | 30 | Dark rum | 30 | Lemonade | 60 | Cranberry juice | 60 | #blend | 0 |  |  | 210 | Big
Hula Hula | baa165 | #crushed ice | 0 | Gin | 60 | Orange Juice | 30 | Triple sec | 5 | #stir | 0 | #strain | 0 |  |  |  |  | 95 | Rock
Judge J Cocktail | ed775f | #crushed ice | 0 | Gin | 60 | White rum | 60 | Lemon juice | 30 | Cranberry juice | 10 | #shake | 0 | #strain | 0 |  |  | 160 | Medium
Rock Bottom | f27157 | Vodka | 60 | Pineapple juice | 10 | Gin | 60 | Lemon juice | 10 | Lime juice | 10 | #shake | 0 | Tequila | 60 |  |  | 210 | Big
Beach Bum Shake | e3a452 | #crushed ice | 0 | Tequila | 30 | Orange Juice | 60 | Vodka | 8 | Triple sec | 5 | #shake | 0 | #strain | 0 |  |  | 103 | Rock
Pussy popper | db5740 | #ice | 0 | Vodka | 90 | Triple sec | 60 | Cranberry juice | 60 | Orange juice | 60 | Grenadine syrup | 5 | #shake | 0 |  |  | 275 | Big
Brass Monkey | f5b922 | Dark rum | 15 | Vodka | 15 | #stir | 0 | Orange juice | 120 | #shake | 0 |  |  |  |  |  |  | 150 | Medium
Legspreader | f0ecd5 | Tequila | 30 | Vodka | 30 | Gin | 30 | Dark rum | 30 | #shake | 0 |  |  |  |  |  |  | 120 | Rock
Liquid Bubble Gum | FFFFFF | Vodka | 60 | Peach Tree | 60 | Cola | 120 | #stir | 0 |  |  |  |  |  |  |  |  | 240 | Big
Desert Sunrise | FFFFFF | #crushed ice | 0 | Vodka | 38 | Orange Juice | 45 | Pineapple juice | 45 | Grenadine syrup | 5 | #stir | 0 |  |  |  |  | 133 | Medium
Absolute Vacation | FFFFFF | #ice | 0 | Cranberry juice | 30 | Orange Juice | 30 | Pineapple juice | 30 | Vodka | 30 | #shake | 0 |  |  |  |  | 120 | Medium
Hawaiian Seduction | FFFFFF | #ice | 0 | Tequila | 30 | Lime juice | 180 | Vodka | 30 | #stir | 0 |  |  |  |  |  |  | 240 | Big
Hawaiian Sea Breeze | FFFFFF | #ice | 0 | Vodka | 45 | Pineapple juice | 135 | Cranberry juice | 10 | #stir | 0 |  |  |  |  |  |  | 190 | Big
Island Punch | FFFFFF | #ice | 0 | White rum | 30 | Grenadine syrup | 5 | Orange juice | 120 | Pineapple juice | 120 | #stir | 0 |  |  |  |  | 275 | Big
Jamaican Sunrise | FFFFFF | Orange juice | 135 | Vodka | 60 | Peach Tree | 60 | #shake | 0 | Cranberry juice | 30 |  |  |  |  |  |  | 285 | Big
Montana Sunrise | FFFFFF | #ice | 0 | Grenadine syrup | 23 | Orange Juice | 60 | Vodka | 120 | #shake | 0 | #strain | 0 |  |  |  |  | 203 | Big
Pimp Daddy | FFFFFF | #ice | 0 | Tequila | 60 | Vodka | 60 | Lemon juice | 30 | Cranberry juice | 90 | #stir | 0 |  |  |  |  | 240 | Big
Adam Cocktail | FFFFFF | #ice | 0 | Dark rum | 60 | Lemon juice | 30 | Grenadine syrup | 30 | #shake | 0 | #strain | 0 |  |  |  |  | 120 | Rock
Long Island Taxi | FFFFFF | #ice | 0 | Vodka | 60 | Gin | 30 | Tequila | 30 | Dark rum | 30 | Orange juice | 60 | #shake | 0 | #strain | 0 | 210 | Big
Caribe Cosmopolitan | FFFFFF | #ice | 0 | Dark rum | 45 | Cranberry juice | 30 | Triple sec | 30 | Lime juice | 15 | #shake | 0 |  |  |  |  | 120 | Medium
Key West Screwdriver | FFFFFF | Vodka | 60 | Lime juice | 30 | Orange Juice | 150 | #stir | 0 |  |  |  |  |  |  |  |  | 240 | Big
Shark Tank | FFFFFF | Lemonade | 120 | Vodka | 120 | Grenadine syrup | 60 |  |  |  |  |  |  |  |  |  |  | 300 | Big
A Gilligans Island | FFFFFF | Vodka | 30 | Peach Tree | 30 | Orange Juice | 90 | Cranberry juice | 90 | #shake | 0 |  |  |  |  |  |  | 240 | Big
Blind Bat | FFFFFF | Vodka | 120 | Cola | 120 | White rum | 10 | #stir | 0 |  |  |  |  |  |  |  |  | 250 | Big
Hot Sex Cocktail | FFFFFF | #ice | 0 | Triple sec | 75 | Orange Juice | 120 | #stir | 0 | Grenadine syrup | 10 |  |  |  |  |  |  | 205 | Big
Bloody Nightmare | FFFFFF | #ice | 0 | Vodka | 30 | Lime juice | 60 | Cranberry juice | 210 | #stir | 0 |  |  |  |  |  |  | 300 | Big
Snoop Dogg | FFFFFF | Gin | 60 | Orange Juice | 90 | #stir | 0 |  |  |  |  |  |  |  |  |  |  | 150 | Medium
Gin Citric | FFFFFF | #ice | 0 | Gin | 60 | Grenadine syrup | 5 | Lemon juice | 30 | Lime juice | 30 | Orange juice | 60 | #stir | 0 |  |  | 185 | Big
Cat Cocktail | FFFFFF | #ice | 0 | Vodka | 45 | Triple sec | 15 | Cranberry juice | 120 | #stir | 0 |  |  |  |  |  |  | 180 | Medium
Hard Dick | FFFFFF | Vodka | 30 | Gin | 30 | White rum | 30 | #stir | 0 | Sprite | 90 |  |  |  |  |  |  | 180 | Medium
Vodka soda | 964B00 | #ice | 0 | Vodka | 60 | Cola | 240 |  |  |  |  |  |  |  |  |  |  | 300
Rum and coke | 964B00 | Cola | 120 | White rum | 50 | Lime juice | 10 |  |  |  |  |  |  |  |  |  |  | 180
Margarita | 42F595 | Triple Sec | 30 | Lime juice | 30 | Tequila | 60 |  |  |  |  |  |  |  |  |  |  | 120
 |  |  |  |  |  |  |  |  |  |  |  |  |  |  |  |  |  | 0
 |  |  |  |  |  |  |  |  |  |  |  |  |  |  |  |  |  | 0
 |  |  |  |  |  |  |  |  |  |  |  |  |  |  |  |  |  | 0
 |  |  |  |  |  |  |  |  |  |  |  |  |  |  |  |  |  | 0
 |  |  |  |  |  |  |  |  |  |  |  |  |  |  |  |  |  | 0
 |  |  |  |  |  |  |  |  |  |  |  |  |  |  |  |  |  | 0
 |  |  |  |  |  |  |  |  |  |  |  |  |  |  |  |  |  | 0
 |  |  |  |  |  |  |  |  |  |  |  |  |  |  |  |  |  | 0
 |  |  |  |  |  |  |  |  |  |  |  |  |  |  |  |  |  | 0
 |  |  |  |  |  |  |  |  |  |  |  |  |  |  |  |  |  | 0
 |  |  |  |  |  |  |  |  |  |  |  |  |  |  |  |  |  | 0
 |  |  |  |  |  |  |  |  |  |  |  |  |  |  |  |  |  | 0
 |  |  |  |  |  |  |  |  |  |  |  |  |  |  |  |  |  | 0
 |  |  |  |  |  |  |  |  |  |  |  |  |  |  |  |  |  | 0
 |  |  |  |  |  |  |  |  |  |  |  |  |  |  |  |  |  | 0
 |  |  |  |  |  |  |  |  |  |  |  |  |  |  |  |  |  | 0
 |  |  |  |  |  |  |  |  |  |  |  |  |  |  |  |  |  | 0
 |  |  |  |  |  |  |  |  |  |  |  |  |  |  |  |  |  | 0
 |  |  |  |  |  |  |  |  |  |  |  |  |  |  |  |  |  | 0
 |  |  |  |  |  |  |  |  |  |  |  |  |  |  |  |  |  | 0
 |  |  |  |  |  |  |  |  |  |  |  |  |  |  |  |  |  | 0
 |  |  |  |  |  |  |  |  |  |  |  |  |  |  |  |  |  | 0
 |  |  |  |  |  |  |  |  |  |  |  |  |  |  |  |  |  | 0
 |  |  |  |  |  |  |  |  |  |  |  |  |  |  |  |  |  | 0
 |  |  |  |  |  |  |  |  |  |  |  |  |  |  |  |  |  | 0
 |  |  |  |  |  |  |  |  |  |  |  |  |  |  |  |  |  | 0
 |  |  |  |  |  |  |  |  |  |  |  |  |  |  |  |  |  | 0
 |  |  |  |  |  |  |  |  |  |  |  |  |  |  |  |  |  | 0
 |  |  |  |  |  |  |  |  |  |  |  |  |  |  |  |  |  | 0
 |  |  |  |  |  |  |  |  |  |  |  |  |  |  |  |  |  | 0
 |  |  |  |  |  |  |  |  |  |  |  |  |  |  |  |  |  | 0
 |  |  |  |  |  |  |  |  |  |  |  |  |  |  |  |  |  | 0
 |  |  |  |  |  |  |  |  |  |  |  |  |  |  |  |  |  | 0
 |  |  |  |  |  |  |  |  |  |  |  |  |  |  |  |  |  | 0
 |  |  |  |  |  |  |  |  |  |  |  |  |  |  |  |  |  | 0
 |  |  |  |  |  |  |  |  |  |  |  |  |  |  |  |  |  | 0
 |  |  |  |  |  |  |  |  |  |  |  |  |  |  |  |  |  | 0
 |  |  |  |  |  |  |  |  |  |  |  |  |  |  |  |  |  | 0
 |  |  |  |  |  |  |  |  |  |  |  |  |  |  |  |  |  | 0
 |  |  |  |  |  |  |  |  |  |  |  |  |  |  |  |  |  | 0
 |  |  |  |  |  |  |  |  |  |  |  |  |  |  |  |  |  | 0
 |  |  |  |  |  |  |  |  |  |  |  |  |  |  |  |  |  | 0
 |  |  |  |  |  |  |  |  |  |  |  |  |  |  |  |  |  | 0
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

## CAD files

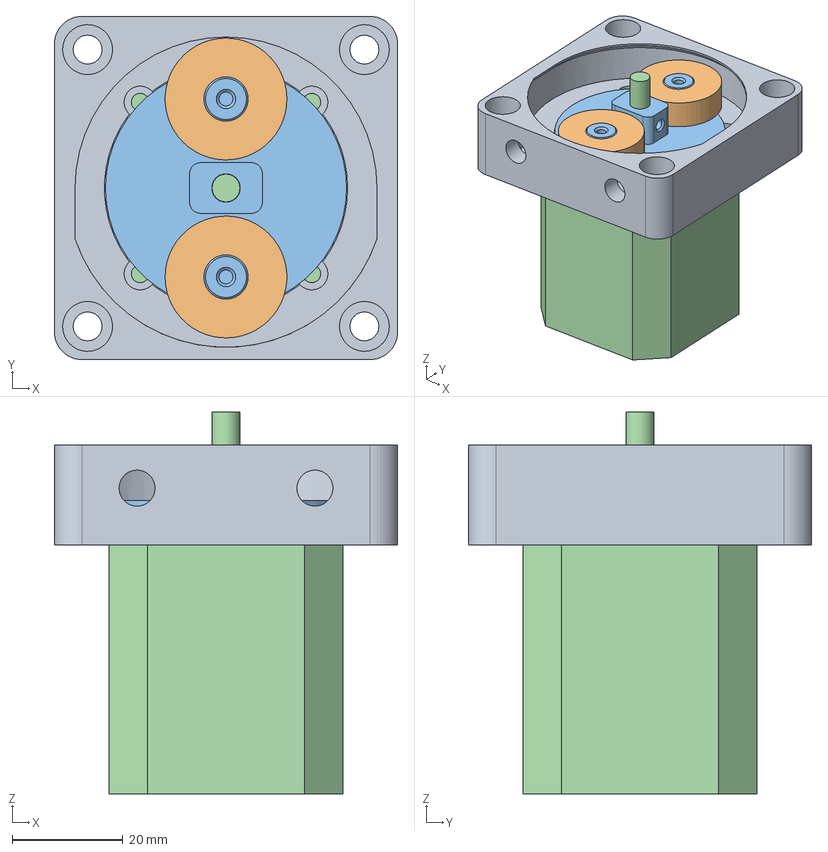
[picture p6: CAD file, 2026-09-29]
CAD/Perestaltic.FCStd
62.0 x 62.0 x 69.0 mm
Bearings 608
Body bearing place adapter
Nema17

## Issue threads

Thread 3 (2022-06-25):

X gantry belt holder

jellewie, 2022-06-25:
X gantry belt holder needs to be more back into the slot, or at least some extensions at the belt point, the belt now pushes against the rollers

Closed 2022-07-06.

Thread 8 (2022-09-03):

squising GoTo button

jellewie, 2022-09-03:
The GoTo button can be squised when on a small screen. This doesn't look nice

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

Closed 2022-09-11.

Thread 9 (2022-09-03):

Custom drink list order

jellewie, 2022-09-03:
Can we either remove the "Actions" list or move it below the "Ingredients"? 99% -if it is even not 100%- of the time you want to add ingredients and not actions

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

Closed 2022-09-11.

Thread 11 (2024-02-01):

Sort CAD dispensers types into into folders

jellewie, 2024-02-01:
Move different types (Already named in code, see "TypeE") of dispensers into there own CAD folder
Or change the name of the file to the type, and put them into a "Dispenser" folder

For example
`Arduino-CocktailMachine/CAD/Parts/Pump plate.FCStd` -> PUMP
`Arduino-CocktailMachine/CAD/Parts/Dispser holder.FCStd` ->SHOTDISPENSER

jellewie, 2024-02-07:
Don't forget to update the Assambly.FCStd too

Closed 2024-02-08.

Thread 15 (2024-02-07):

Pump mounting plate breaks quickly

jellewie, 2024-02-07:
Pump plate.FCStd (will be renamed/moved see #11) breaks quite often in the part that is against the wooden back plate. This is due to layer adhesion, Can we improve this? Like making that part shorter, and or wider

Closed 2024-02-08.

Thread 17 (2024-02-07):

Readme - Add LED strip status

jellewie, 2024-02-07:
For example:

The LED strip will:
- Blink on boot
- Show when homing (ColorHoming)
- Show when homing failed (ColorHomeFail)
- Show a rainbow to signal we are done and IDLE
- Show with dispenser is currently being processes/selected (ColorMoveBase + ColorMoveActive)

jellewie, 2024-02-07:
I believe there was also a feature buildin, that the LEDs would dimm after its been in IDLE mode for some time

Selbiecookie, 2024-02-07:
Fixed with > c44c4b4

Closed 2024-02-07.

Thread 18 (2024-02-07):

The ultimate dispenser project

jellewie, 2024-02-07:
The PUMP dispenser has the problem of that it is not possible for coke and such, since those auto expand and we have a open connection to the outside, so the drink will spill out and run flat.

The SHOTDISPENSER has the issue that it can not do plastic bottles, and even with glass ones it sometimes does not fill the reservoir.

This ticket is there to discuss and track new ideas and types that could overcome these issues. and would be able to dispense coke

jellewie, 2024-02-07:
I have designed a new type of bottle nozzle, this has 2 tubes. One for air to go in, and one for fluid to go out. This would fit on most bottles. [Not in this REPO yet]

Selbie has ordered some valves for testing, it we could mount these below the new nozzle on both sides. If we can mount these on both tubes, this could solve the issue (If the valves are save and work good)

Selbiecookie, 2024-02-07:
Ordered 3 types of solenoid valves (all 12VDC versions), will check out if those can work as a complete replacement for the current dispensers:
- https://aliexpress.com/item/1005005779624351.html
- https://aliexpress.com/item/1005005469057504.html
- https://aliexpress.com/item/1005002876609358.html

Have to check out how they work mechanically, since it has to be food safe, and we do not want any lubricant or other potential harmful substances to enter the liquid that goes through it.

jellewie, 2024-02-08:
Maybe we can re-use the mounting from the Rack assembly, This would make it easy to quick-mount the bottles (bottom and top) and we wouldn't need to design that.

On the other hand, we would still require the valves to be connected to the nozzle, so the unit wouldn't be easily taken off. Unless we design something more for that too? Maybe an even more ideal one is to give the dispenser a little board to send the ID to the main board (same as PNP machines do it) so the machine knows which bottle is connected where (Which bottle ID is which drink settings). And we do not need to manually track that? But this would require quite some engineering in the code, but also in CAD so in the end we might not use them anyway.

jellewie, 2025-03-24:
V2 is here \0/

Closed 2025-03-24.

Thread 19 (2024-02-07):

Front display knob different colour

Selbiecookie, 2024-02-07:
It would be nice if the button had a different more distinct colour

Selbiecookie, 2024-02-07:
https://aliexpress.com/item/1005004402417173.html

Ordered 1 knob:
Blue-White
3-6VDC
22mm
Momentary Reset

Selbiecookie, 2024-02-07:
New button does pose possible clearance problems with the current design of the Display and button holder.

If needed, redesign the Display and button holder. Possibly on a different location, etc.

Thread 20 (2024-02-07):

Infill for profiles to prevent the need of cleaning

Selbiecookie, 2024-02-07:
Find some rubber, or printable things to put inside the V profile. This way you prevent debris from getting in the profile, and having the need to clean it out.

Selbiecookie, 2024-02-07:
https://aliexpress.com/item/1005002971804280.html

2 * 70,5cm for back profile
2 * 34cm for side profiles top
2 * 36cm for side profiles side
Total = 251cm (2,51m)

All other profiles either have belts or wheels in/on them. Also don't need to fill the bottom sides of the profiles since they wont get any dirt in them.

Order 2 lengths of 2 meters in order to have sufficient length to cover the to-be-filled area.

Closed 2025-03-24.

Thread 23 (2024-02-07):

Update/Redesign PCB Schematic + Layout

Selbiecookie, 2024-02-07:
Update/Redesign PCB Schematic + Layout:
- Re-route traces/connections
- Add more pump circuits
- Add input for sensor for glass detection

jellewie, 2024-02-08:
Can we rename the "pump" in the schematic to a more universal one like for example "switching output"?

jellewie, 2024-02-08:
#18 The idea has come up that it could be nice if the mainboard was aware which DispenerID is connected to which slot. This would also require an input multiplexer.

I would like to use the CD74HC4067SM96 (Its in my EasyEda lib) to use as the input multiplexer. I believed this one also had the option to be used as an output multiplexer, but we need to test that.

with 4 select wires, 1 data one. and then 2 for the enable pin on 2 units, we can have 16 inputs and 16 outputs (When not used at the same time, which is what we do)

jellewie, 2025-03-24:
Work in progress, we need 3 new PCB types

jellewie, 2025-04-18:
PCB's desiged and underway for testing

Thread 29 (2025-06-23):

Update website

jellewie, 2025-06-23:
- [x] Show SET error
Make handle_Set command errors include the error code returned
server.send(400, "text/plain", ERRORMSG);

- [x] Change dispenser settings screen
The format is now "LocationX, LocationY, TimeMSML, DelayAir, IngredientID"

- [x] Change /GET format
The /GET has a different format, see /Arduino/Primary/handler.ino handle_Get()
Here an (simulated) example how data could look like
`{"dispensers":[[10,40,40,0,1],[30,40,40,0,2]],"ingredients":["UNK","TRIPLE_SEC","GIN","LIME_JUICE","LEMON_JUICE","LEMONADE","CRANBERRY_JUICE","VODKA","PEACH_TREE","WHITE_RUM","DARK_RUM","TEQUILA","GRENADINE_SYRUP","COLA","SPRITE","ORANGE_JUICE","PINEAPPLE_JUICE"],"settings":{"homed":true,"disablesteppersafteridles":60,"bedSizeX":23950,"bedSizeY":7100,"manualX":23950,"manualY":7100,"motorMaxSpeed":5500,"motorMaxAccel":3000,"homeMaxSpeed":200,"MaxHomeBounce":200,"maxGlassSize":300,"maxBrightness":128,"DispenserHeartbeatS":60}}`

- [x] Change dispenser set settings command
To change dispenser settings (Please only send if value has changed), an SET command can be used:
#define PreFixSetDispenserID "di" 				//Integer>=0, its the number in the array
#define PreFixSetDispenserIngredientID "dn"	//Will need to be send to dispenser itself and will take more time
#define PreFixSetDispenserX "dx"
#define PreFixSetDispenserY "dy"
#define PreFixSetDispenserDelayAir "do"		//Will need to be send to dispenser itself and will take more time
#define PreFixSetDispenserTimeMSML "dl"		//Will need to be send to dispenser itself and will take more time

- [x] Update dispensers list periodically
The setting "DispenserHeartbeatS" which would store in seconds how often the Dispenpensers would be polled. Ideally the interface should reflect these changes.

jellewie, 2025-06-23:
@jespertheend if you want me to include SlotID to dispensers GET command let me know, currently they will be in the order of SlotID (they start from slot 1 to 21, so currently 20 units)

Closed 2025-06-29.

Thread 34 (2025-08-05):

Wait for User sometimes skips waiting for button

jellewie, 2025-08-05:
The "WaitForUser" sometimes just instantly skips

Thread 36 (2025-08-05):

Make wifi resetable

jellewie, 2025-08-05:
Make it so you can make it forget the WiF without the webpage.
This is so you can try if a wifi has "client isolation" off.
maybe something like holding down the button while booting?

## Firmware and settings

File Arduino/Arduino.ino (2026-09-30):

/*
  Program written by JelleWho https://github.com/jellewie
  Board: https://dl.espressif.com/dl/package_esp32_index.json
*/

#include <AccelStepper.h>  //Make sure to install AccelStepper V1.64(+) manually //https://www.airspayce.com/mikem/arduino/AccelStepper/classAccelStepper.html#a68942c66e78fb7f7b5f0cdade6eb7f06

enum PumpMode { OFF,
                PRIME,
                UNLOAD,
                DISPENSE };
//OFF= do nothing
//PRIME = Load until sensor is seen, than 1 turn backwards
//UNLOAD = Run motor backwards for 30s to unload all fluid
//DISPENSE = Prime the dispense tube, than dispence the given amount, then retract the extension tube amount again (to avoid dripping)
const uint8_t SampleSize = 16;
const uint8_t PDO_Step = 12;  //Pin Digital Output, Motor step pin
const uint8_t PDO_Dir = 13;   //Motor Direction pin
const uint16_t StepperSpeedMax = 7000;
const uint16_t StepperSpeedMaxPrime = 2000;

struct PumpConfig {
  const uint8_t PDO_Step_enable;
  const uint8_t PDI_Light_Sensor;

  float mlPerRev;
  float PrimeRevolutions;
  PumpMode Mode = OFF;
  PumpMode LastMode = OFF;       //To see if there is an update to process
  bool FluidDetected = false;    //High if there is fluid detected, low if not
  bool FluidUpdateFlag = false;  //If there is a update to process
  uint32_t TargetSteps = 0;
  uint32_t CurrentSteps = 0;
  unsigned long ModeStartTime = 0;

  //Moving average
  uint16_t Samples[SampleSize] = {};  //To store all the measurements in
  uint8_t SampleIndex = 0;            //At what measurement we currently are
  int32_t SampleTotal = 0;            //Save the total value of all our measurements
};
const uint8_t PumpAmount = 1;
PumpConfig Pumps[PumpAmount] = {
  { 14, 15, 1.0, 5 }
};

AccelStepper Stepper(AccelStepper::DRIVER, PDO_Step, PDO_Dir);

void setup() {
  Serial.begin(115200);
  pinMode(PDO_Step, OUTPUT);
  pinMode(PDO_Dir, OUTPUT);
  Stepper.setMaxSpeed(StepperSpeedMax);
  Stepper.setAcceleration(10000);
  for (uint8_t i = 0; i < PumpAmount; i++) {
    pinMode(Pumps[i].PDO_Step_enable, OUTPUT);
    pinMode(Pumps[i].PDI_Light_Sensor, INPUT);
  }
  DisableAllSteppers();
  Serial.println("booted");
}
void loop() {
  static unsigned long LastTimeHandleCommands;
  if (TickEveryXms(&LastTimeHandleCommands, 500))  //Run at muhc lower rate to save processing time
    HandleCommand();
  static unsigned long LastTimeReadSensors;
  if (TickEveryXms(&LastTimeReadSensors, 50))  //Run at lower rate to save processing time and make the sample time width bigger
    ReadSensors();

  UpdatePumps();

  Stepper.run();
}

void ChangeMode(uint8_t pumpId, PumpMode Mode) {
  Pumps[pumpId].Mode = Mode;
  Pumps[pumpId].ModeStartTime = millis();
  Pumps[pumpId].FluidUpdateFlag = true;
}
void HandleCommand() {  //HANDLE COMMANDS, (temp for serial testing)
  if (Serial.available()) {
    String received = Serial.readStringUntil('\n');
    received.trim();  // Removes \r, \n, spaces, etc.
    received.toUpperCase();
    Serial.println("Serial received '" + received + "'");
    if (received == "O") {
      ChangeMode(0, OFF);
    } else if (received == "P") {
      ChangeMode(0, PRIME);
    } else if (received == "U") {
      ChangeMode(0, UNLOAD);
    } else if (received == "E") {
      ChangeMode(0, DISPENSE);
    } else
      Serial.println("HandleCommand unknwown command '" + String(received) + "'");
  }
}
void ReadSensors() {  //Read the sensors and save the average
                      //The first average of SampleSize samples will be junk after a bootup.
  for (uint8_t i = 0; i < PumpAmount; i++) {
    PumpConfig& pump = Pumps[i];
    pump.SampleIndex++;                  //Move index forward
    if (pump.SampleIndex >= SampleSize)  //If we are about to overflow
      pump.SampleIndex = 0;              //Reset index
    //Calculate average sensor reading
    pump.SampleTotal -= pump.Samples[pump.SampleIndex];                  //Remove oldest measurement
    pump.Samples[pump.SampleIndex] = analogRead(pump.PDI_Light_Sensor);  //Set new measurement
    pump.SampleTotal += pump.Samples[pump.SampleIndex];                  //Add new measurement
    uint16_t Average = pump.SampleTotal / SampleSize;
    //Check if a fluid change has happened
    if (pump.Samples[pump.SampleIndex] > Average * 1.05) {         //If we went from no-fluid to fluid
      pump.FluidDetected = true;                                   //Update the value to reflect the detected change
      pump.FluidUpdateFlag = true;                                 //Flag there is an update
    } else if (pump.Samples[pump.SampleIndex] < Average * 0.95) {  //If we went from fluid to no-fluid
      pump.FluidDetected = false;                                  //Update the value to reflect the detected change
      pump.FluidUpdateFlag = true;                                 //Flag there is an update
    }
  }
}
void UpdatePumps() {
  for (uint8_t i = 0; i < PumpAmount; i++) {
    PumpConfig& pump = Pumps[i];
    bool ModeUpdated = false;
    if (pump.LastMode != pump.Mode) {
      pump.LastMode = pump.Mode;
      ModeUpdated = true;
      Serial.println("UpdatePumps pump=" + String(i) + " mode=" + String(pump.Mode));
    }
    switch (pump.Mode) {
      case OFF:
        if (ModeUpdated) {  //If the mode just changed to OFF
          Stepper.stop();
          DisableAllSteppers();
        }
        break;
      case PRIME:
        if (ModeUpdated)  //If the mode just changed
          Stepper.setMaxSpeed(StepperSpeedMaxPrime);
        if (millis() - pump.ModeStartTime > 30000) {  //If there is no fluid detected after running, avoid flooding the whole place and stop
          Serial.println("ERROR, timeout Priming on pump " + String(i));
          pump.Mode = OFF;  //Cancel mode, we timed out
        } else if (pump.FluidUpdateFlag) {
          if (pump.FluidDetected and millis() - pump.ModeStartTime > 100) {  //If fluid detected and running for a bit to avoid startup jerk
            Stepper.stop();                                                  //Stop death here in tracks, dont ramp downt
            MovePumpRevolutions(i, -1);                                      //Move 1 rotation backwards
          } else
            MovePumpRevolutions(i, 100);  //Move forwards
          pump.FluidUpdateFlag = false;
        } else if (Stepper.isRunning() == false)  //If we reached our destination
          pump.Mode = OFF;                        //we are done
        break;
      case UNLOAD:
        if (ModeUpdated) {               //If the mode just changed to OFF
          MovePumpRevolutions(i, -100);  //Emthy the tube backwards
          Stepper.setMaxSpeed(StepperSpeedMax);
        }
        if (Stepper.isRunning() == false)  //If we reached our destination
          pump.Mode = OFF;                 //we are done
        break;
      case DISPENSE:
        uint8_t dispenceAmountRotations = 20;
        uint8_t TubePrimeRotations = 4;
        static bool HasDispenced = false;
        if (ModeUpdated) {                                                       //If the mode just changed
          MovePumpRevolutions(i, TubePrimeRotations + dispenceAmountRotations);  //Prime + dispence the tube to the glass
          HasDispenced = false;
          Stepper.setMaxSpeed(StepperSpeedMax);
        }
        if (Stepper.isRunning() == false)  //If we reached our destination
          if (HasDispenced) {
            pump.Mode = OFF;  //we are done
          } else {
            MovePumpRevolutions(i, -TubePrimeRotations);  //Emthy the tube backwards
            HasDispenced = true;
          }
        break;
    }
  }
}
void MovePumpRevolutions(uint8_t PumpId, float Revolutions) {
  DisableAllSteppers();
  digitalWrite(Pumps[PumpId].PDO_Step_enable, LOW);  //Enable this stepper
  const int StepsPerRev = 1600;                      //We have 1600 steps per full resolution
  long Steps = Revolutions * StepsPerRev;
  Stepper.move(Steps);
}
void DisableAllSteppers() {
  for (uint8_t i = 0; i < PumpAmount; i++)
    digitalWrite(Pumps[i].PDO_Step_enable, HIGH);  //Disable all steppers
}

//Functions:
bool TickEveryXms(unsigned long* _LastTime, unsigned long _Delay) {
  //With overflow, can be adjusted, no overshoot correction, true when (Now < _LastTime + _Delay)
  /* Example:   static unsigned long LastTime;
                if (TickEveryXms(&LastTime, 1000)) {//Code to run}    */
  static unsigned long _Middle = -1;                  //We just need a really big number, if more than 0 and less than this amount of ms is passed, return true)
  if (_Middle == -1) _Middle = _Middle / 2;           //Somehow declairing middle on 1 line does not work
  if (millis() - (*_LastTime + _Delay) <= _Middle) {  //If it's time to update (keep brackets for overflow protection). If diffrence between Now (millis) and Nextupdate (*_LastTime + _Delay) is smaller than a big number (_Middle) then update. Note that all negative values loop around and will be really big (for example -1 = 4,294,967,295)
    *_LastTime = millis();                            //Set new LastTime updated
    return true;
  }
  return false;
}

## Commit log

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2022-07-03 fixes EEPROM writing mistakes
    [Arduino.ino]
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2022-07-03 Bug fixes and inprovements
    [Arduino.ino]
2022-07-03 CAD update
    [Assambly.FCStd, Feed motor.FCStd, Leadscrew moer TR8x8.FCStd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]
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2022-07-03 fix(client): Don't cut off drink images glow at the top of the drink selector
2022-07-05 Revert "Add FastLED code"
    This reverts commit 9dec8d600e127ac2c6c65f3844fc863286560779.
    [Arduino.ino]
2022-07-05 Bug fixes, 3 axis now working
    [Arduino.ino]
2022-07-05 fix(client): Don't focus on text fields when opening customize drink dialog
    This causes the virtual keyboard to pop up on mobile devices
2022-07-05 Some more bug fixing
    [Arduino.ino]
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2022-07-06 fix(client): Close settings dialog when clicking the done button
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2022-07-13 Move Z before XY
    Move the Z down before moving XY,
    Also tried to fix some homing issues
    [Arduino.ino]
2022-07-16 fix(client): Point soft settings button to /ip
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2022-09-03 Dispencer 0 no longer invalid to use
    [Arduino.ino]
2022-09-11 Fix 'go to' button rendering on two lines
    Fixes #8
2022-09-15 Better Dispensers defaults
    [Assambly.FCStd]
2022-09-24 Added LEDs and some fixes
    [Arduino.ino]
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2022-09-25 Timeout AFTER each move
    Dont just start that timer after a mix started, set the timer after each move is done. This would make it a IDLE timer
2022-09-25 small fixes and inprovements
    [Arduino.ino]
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2024-02-01 Update ReadMe.md
    Link to "Website/src/drinksConfig.js." in readme is broken. but file is there
    ReadMe "LED status" need to be re-written
2024-02-07 Added an old file
    might be of use someday
    [Pincher.FCStd]
2024-02-07 #11 renamed files
    not done the update on the assembly
    [PUMP.FCStd, SHOTDISPENSER.FCStd]
2024-02-07 Updated Readme for LED strip
    Updated the Readme file to include LED strip statuses and behavior on specific events.
2024-02-07 Updated BOM
    Edited 2 things in the BOM:
    - Added "20x20" measurements to the v-slots
    - Increased the peristaltic pump amount from 2 to 4
2024-02-07 Moved the files into there own folder #11
    [PUMP.FCStd, SHOTDISPENSER.FCStd]
2024-02-07 Added new Nozzle drawing
    #18
    [Bottle Nozzle.FCStd]
2024-02-08 Updated the assembly
    Close #11
    [Assambly.FCStd, Bottle Nozzle.FCStd, Rack Dispencer.FCStd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]
2024-02-08 Made PUMP-mount wall thicker and shorter
    close #15
    [PUMP.FCStd]
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2024-02-12 Worked on #18
    Added a way of mounting, and added more models.
    More work needs to be done, but we are getting a start
    [Assambly.FCStd, Bottle Nozzle.FCStd, Bottle plug.FCStd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]
2024-09-29 Added dimension to 2D drawing
    [Bottle Nozzle.FCStd]
2024-09-29 Staring new version
    [Bottle Nozzle combo V3.FCStd, Bottle Nozzle.step, Nozzle Mount.FCStd]
2025-03-10 Doublenozzle update (all versions included)
    [Bottle Nozzle V2.FCStd, Bottle Nozzle V2.step, Bottle Nozzle V4.FCStd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]
2025-03-10 Create The Big cocktail mixer machine sheet.xlsx
    [The Big cocktail mixer machine sheet.xlsx]
2025-03-16 init moving to V2
    Nothing is organised, bu
    [X gantry Front-Body.stl]
2025-03-16 First working testing version for new system
    [Bottle Nozzle V2.stl, Bottle Nozzle V6-Bottle Holder.stl, Bottle Nozzle V6-Wall Mount.stl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]
2025-03-16 reorder, sort, and cleanup for V2
    [Bottle Nozzle V2.FCStd, Bottle Nozzle V2.step, Bottle Nozzle V2.stl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]
2025-03-18 Moved to new file structure
    [Bottle Nozzle V6-Bottle Holder.stl, Bottle Nozzle V6.FCStd]
2025-03-18 groundwork for duplex communication
    Duplex communication, adoption, commands, scan ID's, and the
2025-03-22 Attiny support
    This code is bebugable on an ESP32, when the compiler detects you are compiling to an ESP it will change the code to debugging.
    Also tweaked the timers to be faster, found out that the Attiny does not have a problem with this
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2025-03-23 Experimented with speed settings
    These gave 1000/1000 IDs good from ATtiny85 to ESP32
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2025-03-24 Removed Z axis (not used in V2)
    the cut might not be clean, but we need to start somewhere with V2 code
2025-03-24 Fix for comping in linux with new IDE
    [Arduino.ino]
2025-03-24 Updated to Arduino IDE 2.3.4
    Appearenly "client.h" is not allowed in Arduino IDE 2.3.4 anymore? The orginal main code was written in IDE 1.8.16
2025-03-25 starting of merge of V2 dispensers
    Pumps will also get there own mainboard, and respond the same as the new dispensers. so no extra pins/code needed for them here
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2025-03-27 Fixed some stepper problems
    Getting the whole sketch working on the old hardware. Step-direction and homedistanceBounce seem to not yet play alonge
2025-03-28 Faster homing
    it now looks for unpressing the button, no blindly doing stepps.
    Also limited the allowed movement by MoveWait
    renamed HomedistanceBounce to MaxHomeBounce to make its function more clear
2025-03-28 Groundwork to handle frontend
    Standardised some names.
    Layed first hands to make website work with backend.
2025-03-30 Updated CAD model
    Also fixed #25
    [Assambly.FCStd, Bottle Nozzle V6.FCStd, Leadscrew moer TR8x8.FCStd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]
2025-04-02 Updated Y ganrty
    Made it even more easy to print and clean #25
    [Y gantry.FCStd, Z gantry.FCStd]
2025-04-02 File cleaning
    [Bottle Nozzle V6-Bottle Holder.stl, Bottle Nozzle V6-Wall Mount.stl, Bottle Nozzle V6.FCStd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]
2025-04-02 Add step files for CNC part
    [Bottle Nozzle V6-Bottle Nozzle.step]
2025-04-05 Intergrated PCB's
    Intergrated the SLOT and DISPENSER PCB's into the design
    [Bottle Nozzle V6.FCStd]
2025-04-08 Fixed nozzle holder hole being to small
    Also added the new version of PCB's which now also include the TS-1233 button
    [Bottle Nozzle V6.FCStd, TS-1233.FCStd]
2025-04-15 Added Air valve
    [Air Valve WCD130-24B.FCStd]
2025-04-15 Print adoption errors
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2025-04-17 Add Air valve mounting holes
    [Bottle Nozzle V6.FCStd]
2025-04-21 Added pump, better printable holder
    Made the bottle holder 3D print better printable with the holes.
    Added the air valve to the assembly
    [Bottle Nozzle V6.FCStd]
2025-04-21 Updated main assembly
    now it has the new type of nozzles (V2) shown
    [Assambly.FCStd]
2025-04-22 Hardware ID support
    Thanks to @Poeutra for a cup of tea to keep going 😃
    Added the option to set the dispenser ID in hardware, this is for example handy if you want to permanently mount the pumps and not add another SLOT pcb. This change is backwards compatible, and the h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
    [The Big cocktail mixer machine sheet.xlsx]
2025-04-22 Revert TEST-changes that where not asked to be included
    This reverts part of commit cc7e772676c30932c0034ac8cc32577119bed1d9.
    [The Big cocktail mixer machine sheet.xlsx]
2025-05-09 Update assembly and parts
    [Assambly.FCStd, Bottle Nozzle V6.FCStd, PUMP.FCStd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]
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2025-05-11 Tolerances, Mouning air valve, holes for attiny and magnet
    [Bottle Nozzle V6.1.FCStd]
2025-05-14 Added bolt to velcro
    This is so the velcro strap can be hold in place
    [Bottle Nozzle V6.1.FCStd]
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2025-06-09 Fixed timing bug in gettin ID
    Also left behind the ESP32 DOIT pinout for debugging. enable Disp to move from S3 to DOIT
2025-06-09 Dispenser fixes
    Better and more usefull debug text to the LCD screen.
    Removed the PJON_FAIL message from being printed, we do not need to know which slots are not connected
2025-06-22 If SlotID is to big, just stop
    When there is a hardware error and pulses keep comming in, just stop at 255 and call it 'invalid' (0)
2025-06-27 Fixed comma in dispenser list printing
2025-07-03 LED mounting bracked
    [LED mounting.FCStd]
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2025-07-16 Update The Big cocktail mixer machine sheet.xlsx
    [The Big cocktail mixer machine sheet.xlsx]
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2025-07-19 scale FluidLevel to fit in a byte
    Scaler or 10 so from 0ml to 2560ml bottle sizes are now supported for compensation
2025-07-19 fix some serial print typos
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2025-07-20 Fix button scan pulling to be 0.1S
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2025-08-01 Fix debug button naming
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2025-08-01 Getting ready for first V2 release
    [Dispenser V2.3 PickAndPlace.csv, Primary V2.1 PickAndPlace.csv, Slot V2.3 PickAndPlace.csv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]
